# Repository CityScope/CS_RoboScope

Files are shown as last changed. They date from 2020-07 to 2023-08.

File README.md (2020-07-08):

# RoboScope

RoboScop project is an motorize platform and three-dimensional interactive simulation platform for the understanding of urban environments. The platform is made of an array of 3D Pixels that can be configured in varying heights and color to represent different urban conditions. In addition, each pixel

## Circuits

Circuits designs in Eagle

## Code

Source code to run the each one of the different project components, server, client, control and interface.

## Docs

Folder includes designs files, drawings, technical data-sheets, and assembly instructions.

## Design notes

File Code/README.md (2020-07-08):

# Source

Source code for each one of the following components:

- Interface App

  Interface Apps are the applications that act as an interpreter between the physical table and the digital platform. The applications have two versions: a standalone WebApp and a local application in Processing or openFrameworks.

- Hardware

  Code that runs on the physical hardware such as motor control modules, server can bus module, and test code to test hardware.

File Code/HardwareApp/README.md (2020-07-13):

# Hardware Apps

Arduino

## Translator App

Application that manages and translates grid information to the motor modules.

## Module App

Client application for each board.

## Libraries

List of Arduino libraries

- SX1509
- NeoPixel
- CAN Bus FD FlexCAN

## Test Code

- CanBus

- EnableMotor

- NeoPixel

- MotorTest

- InteractionTest

### CAN Bus Protocol

- 11-bit Motor id identifier
- CAN Bus Message - 4 byte Protocol
  - 2 byte RGBW Color
  - 1 byte Motor position
  - 1 byte interaction

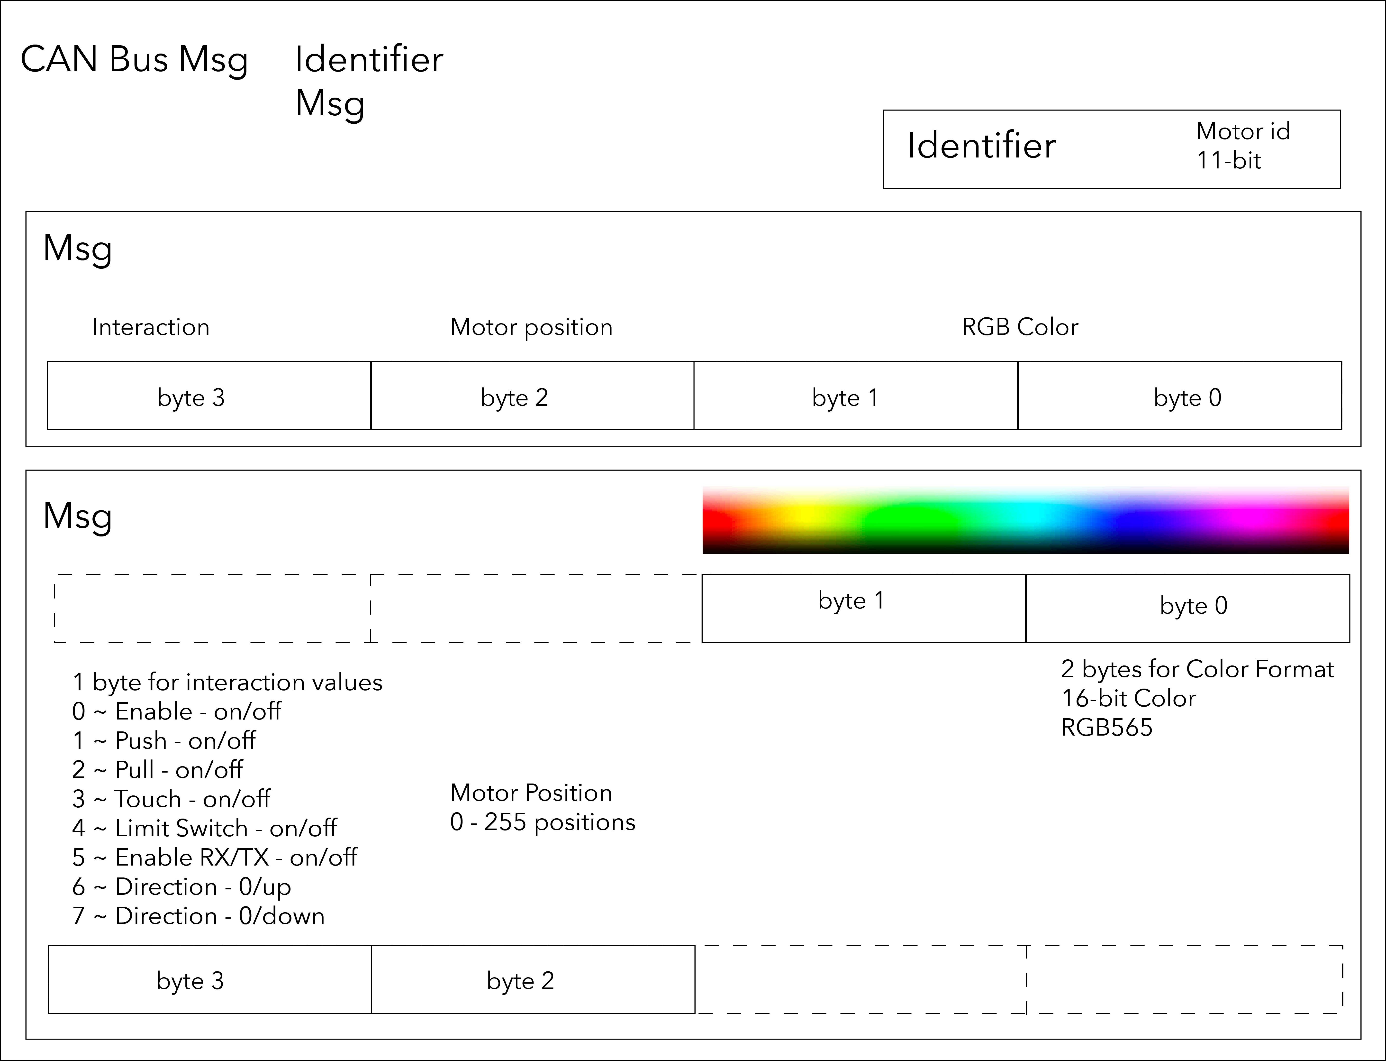
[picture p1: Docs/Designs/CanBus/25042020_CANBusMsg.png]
CAN Bus Block


Server will

  - Board id
    - [id] -> uint32_t
    - ````4 bytes -> [0-4294967295] or [0x00000000-0xFFFFFFFF]````
  - Message
    - buf[8] -> uint8_t array length 8
    - ````1 byte -> [0-255] or [0x00-0xFF]````
      - [0] - Motor id [0, 255]
          - Local id depending on the number of motors on the board
      - [1] - Motor dir - up/down
      - [2] - Motor step  - number of steps
      - [3] - Motor time activation
      - [4] - Motor enable/sleep/activation
      - [5] - Motor limit switches and push and pull
          - ```[0000LHDU]```
          - Limit switch up   (U)    ```[0000000U]```
          - Limit switch down (D)    ```[000000D0]```
          - Push Interaction (Push)  ```[00000H00]```
          - Pull Interaction (Pull)  ```[0000L000]```
      - [6] - Motor sensor 0
      - [7] - Motor sensor 1

### Library:

  - CAN Bus FD and CAN Bus 2.0 for  Teensy 4.0
    https://github.com/tonton81/FlexCAN_T4

  - Data Structure:
    CAN Bus 2.0
    https://github.com/collin80/FlexCAN_Library

  - CAN Bus FD - MCP2562FD
    https://www.microchip.com/wwwproducts/en/MCP2562FD

### Refereces:

  https://github.com/skpang/Teensy40_triple_CAN_demo/blob/master/Teensy40_triple_CAN_demo.ino

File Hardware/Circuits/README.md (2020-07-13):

#  PCB design

## Motors driver

- Teensy 4.0
  - https://www.pjrc.com/store/teensy40.html
- 8 Stepper Motor Drivers
  - DRV8880
  - https://www.pololu.com/product/2971
- Two voltage inputs
  - 12V Input
  - 5V Input, Voltaje protection
- CAN Bus FD  JST Input/Output
  - https://www.digikey.com/short/zb3m2n
- CAN Bus 2.0 JST Input/Output
  - https://www.digikey.com/short/zb3mwz
- SX1509 Multiplexer
  - https://www.sparkfun.com/products/13601
- On/Off Switch

## Interface

- 8x Push Buttons
- 8x 6 Pin JST 1mm
- 3x SX1509 Multiplexer
- Dip Switches

## LED Box

- 4 RGBW LEDs, SK6812
- 2 Push buttons
- JST 1mm

## Translator

- JST 6 pin limit output 1mm
- 4 Key buttons
- CAN Bus 2.0 JST Input/Output
  - https://www.digikey.com/short/zb3mwz
- SX1509 Multiplexer
  - https://www.sparkfun.com/products/13601

## Stepper Counter

- Switch
- JST 1mm
-

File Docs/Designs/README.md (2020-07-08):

# Design files

Core

Fusion 360

## v.02

### Base

- Adjust spacing of the holes of the base
- Adjust the base for each motor, opening for each motor, cable pass for each motors

## Aesthetics

- Box design

### Interface Box

- Redesign the box

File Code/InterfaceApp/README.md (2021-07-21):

## CS CityScope JS

Application in js that allows users to examine different urban-design alternatives and observe their impact through different KPIs and matrices.

### Instructions

##### Running CityScope JS
To run the web application, you can go to the [CityScope JS](https://cityscope.media.mit.edu/CS_cityscopeJS/) website or download/clone the repo here and run the app locally.

To run the app locally, run `npm install` inside the folder to install all the packages and then run `npm start`. For more documentation, go to [CityScope ](https://cityscope.media.mit.edu) website.

##### Roboscope path

`http://localhost:3000/cityscope=roboscope`

##### Setting Up Table Controller
1. Download/clone repo and `cd` into DigitalControls in Terminal
2. Install packages
    1. python-socketio version 4.5.1
    2. flask-socketio 4.3.0
      `pip install python-socketio==4.5.1`
      `pip install flask-socketio==4.3.0`
    2. eventlet version 0.25.2
    3. Flask
3. Connect Teensy table server
4. In `grid_handling.py` change `com_port` to port connected to table server
5. Run `python3 websocketServer.py`

## Virtual Serial Port

Create a virtual port to test communication between the WebSocket and the serial port.

### Mac

`pip3 install PyVirtualSerialPorts`

## Create a Virtual Port

`python3 -m virtualserialports 1`

`ls /dev/cu.*`

## Blocks App

Application in Processing that simulates the physical table

## MovingLegosServer App

Application in openFrameworks that simulates the physical table

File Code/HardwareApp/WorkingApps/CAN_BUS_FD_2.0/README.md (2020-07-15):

## A working implementation of the CAN Bus Protocol 

This implementation of the CAN bus protocol has two parts: server and client. Each utilizes a Message class that was created with the data protocol designed for the Roboscope table. 

### Message Class

The message class provides a seamless way to customize and format CAN bus messages before they are sent to the client or to the server. The following outlines the functions of the class and their uses:
 
- `CANMotorMessage(panel_id, msg_size = 8)`: initializes a CAN bus message with a give panel (node) ID, the msg_size determines whether to send a CAN_FD msg or CAN 2.0 msg
- `addMessage(des, color[], steps, interaction)`: adds 4 bytes of data (color, motor steps, and interaction byte) to its appropriate spot in the message buffer array as determined by the specific motor ID the data is referring to
- `getCANmessage()`: returns a CAN bus message that can then be written to a client

### CANFD_Server

The server writes CAN bus message to the client. The current program sets up CAN bus FD and 2.0, initializes input (button) and output (LED) features, and sends a hardcoded CAN bus message to the client on a button press. 

### CANFD_Client

The client reads CAN bus message from the server. The current program sets up CAN bus FD and 2.0, initializes input (button) and output (LED) features, and prints out all CAN bus messages when received from the server

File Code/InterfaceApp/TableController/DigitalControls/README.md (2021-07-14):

# Web Socket Server

This server is the layer of communication between the Interface App and the physical Roboscope table. The server uses web sockets to send and receive data to and from the Interface App and uses serial communication with the Translator Teensy. Current functionality allows grid updates from the JS Interface while 'brushing' edit events occur to be sent to Translator and continuous reading of data from Translator.

## websocketServer.py

This main server file sets up communication with and runs the sockets that connect to the Interface App. For more information about sockets and socket.io, check out the documentation for the [python-socketio library](https://python-socketio.readthedocs.io/en/latest/)

## grid_handling.py

This file is for all computation and data processing methods needed to be able to send the proper data to either the InterfaceApp or the physical table.

## Install & run

-   run `$ npm install`

-   pyhon 3.3, install Flask, socketio

    `$ pip install flask`

    `$ pip install socketio, python-socketio`

    `$ pip install eventlet, npm, colour, gevent`

-   Run the server with `python websocketServer.py`

Connect to roboscope:

http://localhost:3000/cityscope=roboscope

### Troubleshooting

- Kill Process:

Find the process using port 8080:

`sudo lsof -i:8080`

Kill the process on that port:

`kill $PID`

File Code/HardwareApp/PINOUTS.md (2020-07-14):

# PINOUTS

The pinouts for all the hardware components to be used in code.

## Wiring guide for connecting the motors to the motor control Board

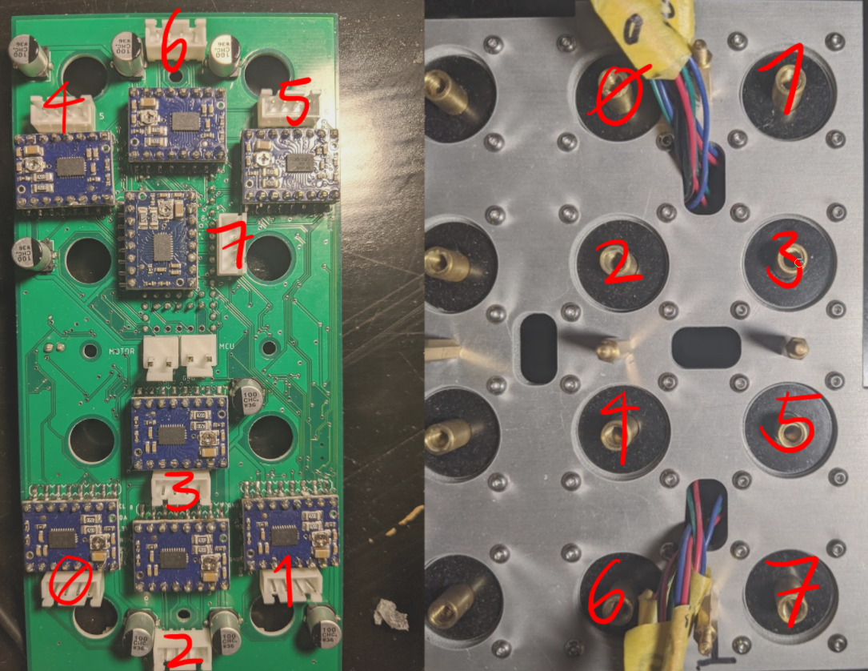
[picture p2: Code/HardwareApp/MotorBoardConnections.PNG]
Motor Wiring Guide


## Pinouts per pixel

| | **Pixel** |  0 |  1 |  2 |  3 |  4 |  5 |  6 |  7 |
|:---:|:---:|:--:|:--:|:--:|:--:|:--:|:--:|:--:|:--:|
| **Pin** | | | | | | | | | |
| Motor Direction | |  6 |  8 | 10 | 15 | 17 | 21 | 23 | 25 |
| Motor Step | |  5 |  7 |  9 | 14 | 16 | 20 | 22 | 24 |
| SX1509 Limit Switch | | 15 | 14 | 13 | 12 | 11 | 10 |  9 |  8 |
| SX1509 Interaction Switch | |  7 |  6 |  5 |  4 |  3 |  2 |  1 |  0 |

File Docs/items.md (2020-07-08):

## List

8/18

Final list of items to buy:
https://docs.google.com/spreadsheets/d/1OweoeCU06feMGqQnCsFGZUhG3TEGoh_JW88oVjHfxHk/edit#gid=0

### Base

- design files of the base
- matrix design files
- Rubber Bushings for base
- screws for motors
- acrylic for top
- aluminum plate for the matrix
- aluminum plate for bottom plate (electronics)
- 3d model of the spacer

Instead of matrix grid approach for the base, Kent suggest we should do horizontal or vertical modules, for easier remove, adjust and plug-play approach.

### Rods/Box

- switches
  - https://www.mouser.com/ProductDetail/653-D2F-01L2-T
- LEDs RGBW
  - NeoPixel:
    https://www.adafruit.com/product/2758
- qwiic cables JST-4 Cable
- 3d Model of the Box
- sensor to detect touch
- Pull/Push interaction

## Energy

Teensy module
  - 4 Amps

## Controls

 - Voltage Control:
   - Arduino ->
   - LEDs
   - Motor
   - Sensors

 - Motor control https://www.sparkfun.com/products/12779
    - STEP    -> GPIO Arduino
    - DIR    -> GPIO Arduino
    - ENABLE -> GPIO Arduino
    - MS1 -> switch GND or 5V
    - MS2 -> switch GND or 5V
    - Voltage IN  -> Power supply range from 6V to 30V.
    - Voltage OUT -> regulated 5V

- Motor Driver:
    - STSPIN220 Low-Voltage Stepper Motor Driver Carrier,  1/256 step https://www.pololu.com/product/2876
    - DRV8834 - 1/32 step https://www.pololu.com/product/2134/specs

 - CAN Bus Protocol (5V, GND)
    - MCP2515  with TJA1050
        - https://harrisonsand.com/static/CAN_module.pdf
    - SCK, MOSI, MISO
    - D13 -> SCK - SCK
    - D12 -> SO  - MISO
    - D11 -> SI  - MOSI
    - D10 -> CS  - ANY
 - swiic cable model
 - voltage input 5V
 - Teensy 3.2 -> CAN BUS, I2C
 - LED for power status
 - switch to turn on/off the motor
 - enumerate each motor and sensor output
      -
 - SAMD21  + 48mhrz
    - https://www.sparkfun.com/products/13664
    - https://www.avdweb.nl/arduino/samd21/samd21-programmer
 - DIP Switch for changing the ID of the motor
    - DIP 10 positions -> 2^9
      https://www.sparkfun.com/products/8034
    - Multiplexer   16 channels
      https://www.sparkfun.com/products/9056
  - CAN Bus Output
  - Switch's Control
      - SparkFun 16 Output I/O Expander Breakout
      - https://www.sparkfun.com/products/13601

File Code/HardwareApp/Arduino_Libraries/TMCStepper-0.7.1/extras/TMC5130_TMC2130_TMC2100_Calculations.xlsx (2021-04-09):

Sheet: Velocity Calculation
This spreadsheet allows the calculation of target velocity and acceleration values for the internal ramp generator of the TMC5130
Usage: | 1. First enter the highlighted values in Parameters and settings
 | 2. Now you can use one of the calculations (1. - 4.) by entering the known parameters (green)
Parameters and settings
 | 150 | RPM | Desired Velocity | t | = | 2^24/fCLK | = | 1.048576 | [sec]
 | 16 | µS/FS | µStepresolution (256) | VMAX | = | 0 … 2^23-512 |  | [µS/t]
 | 1.8 | ° | Fullstep angel | fCLK | = | 16000000 |  | Hz
 | 200 | FS/360° | Fullsteps per revolution
 | 3200 | µS/360° | µSteps per revolution
 | 1 | :1 | gear ratio
1. VMAX to real world units
 | 8388.608 | VMAX | [µS/t] | <--Entry desired VMAX setting here!
 | 2.50 | RPS | motor shaft
 | 900.00 | deg/sec | motor shaft
 | 900.00 | deg/sec | gear box out
 | 8000.00 | Hz | [µSteps/s]
 | 2.50 | RPS | gear box out
2. real world units to VMAX
 | 2.50 | RPS | motor shaft | <--Entry desired rotations per second here!
 | 900.00 | deg/sec | motor shaft
 | 8388.608 | VMAX | [µS/t]
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

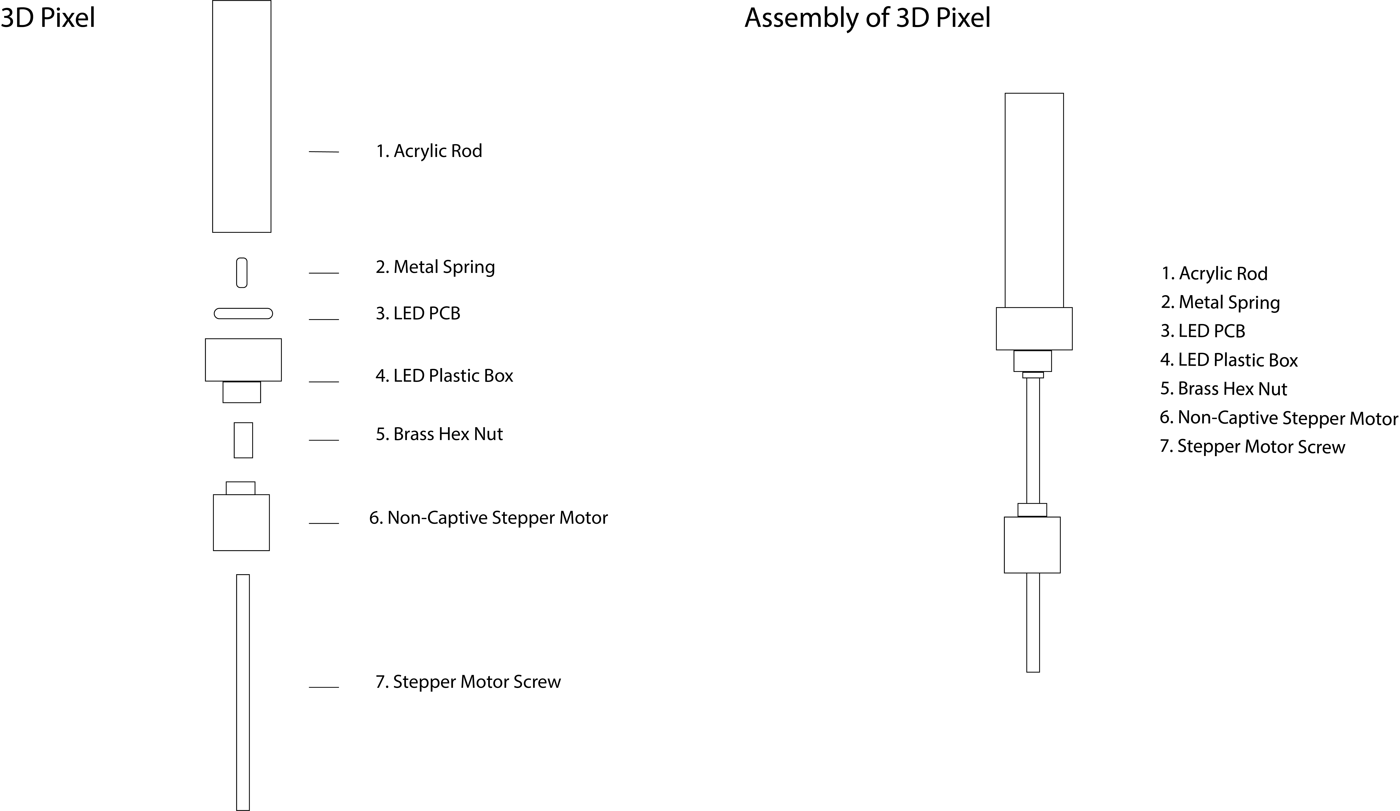
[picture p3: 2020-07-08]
Docs/Designs/Grids/25042020_UrbanPixelDesign.png

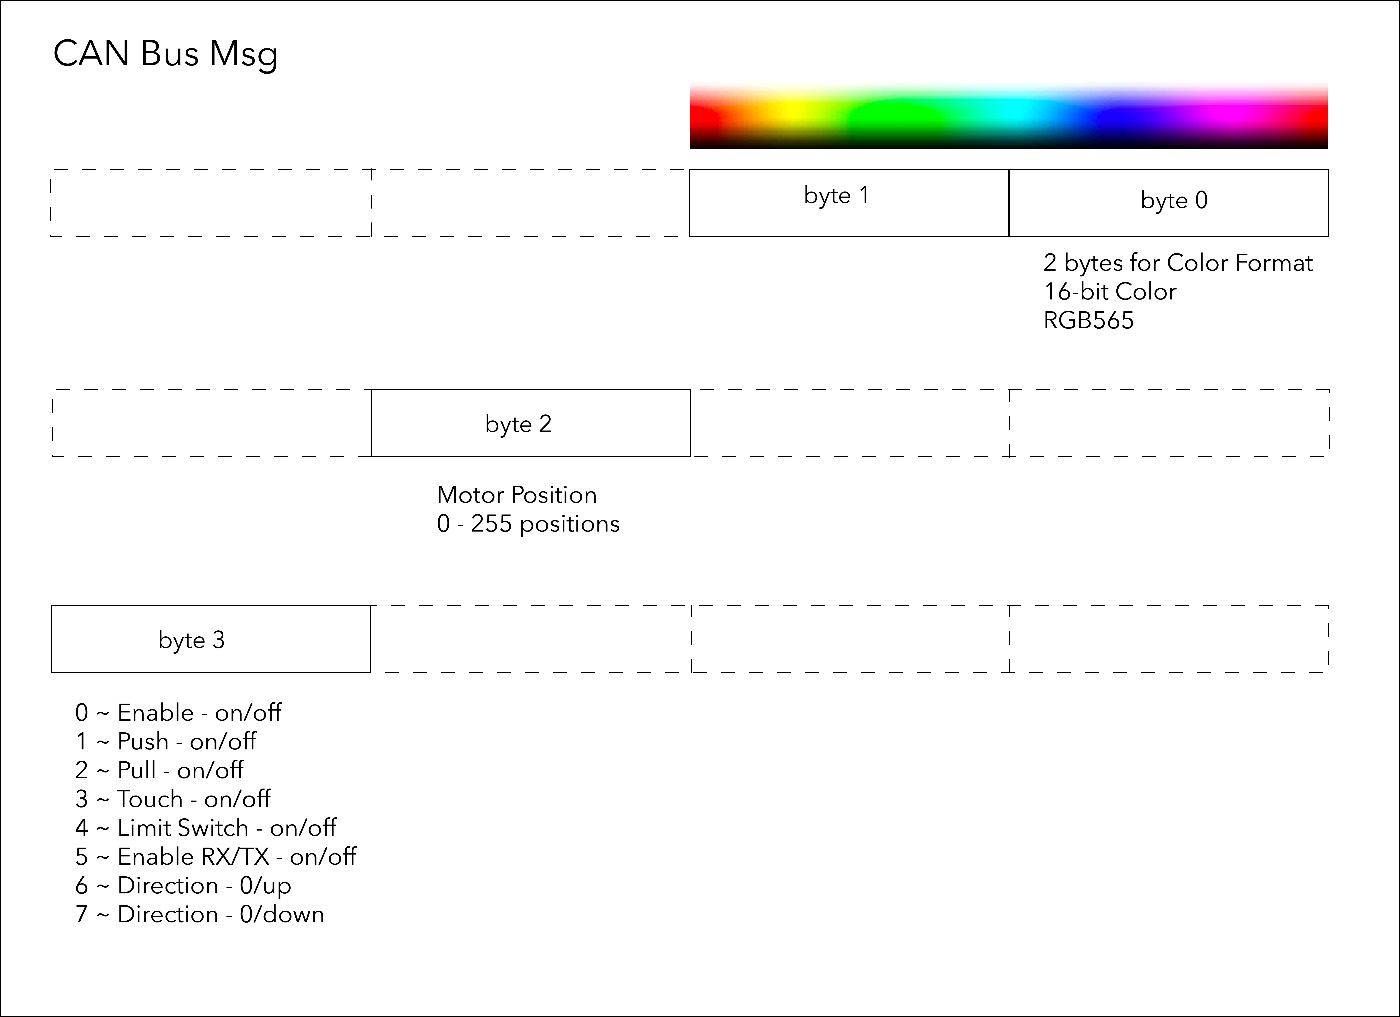
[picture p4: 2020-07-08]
Docs/Designs/CanBus/25042020_CANBusData.png

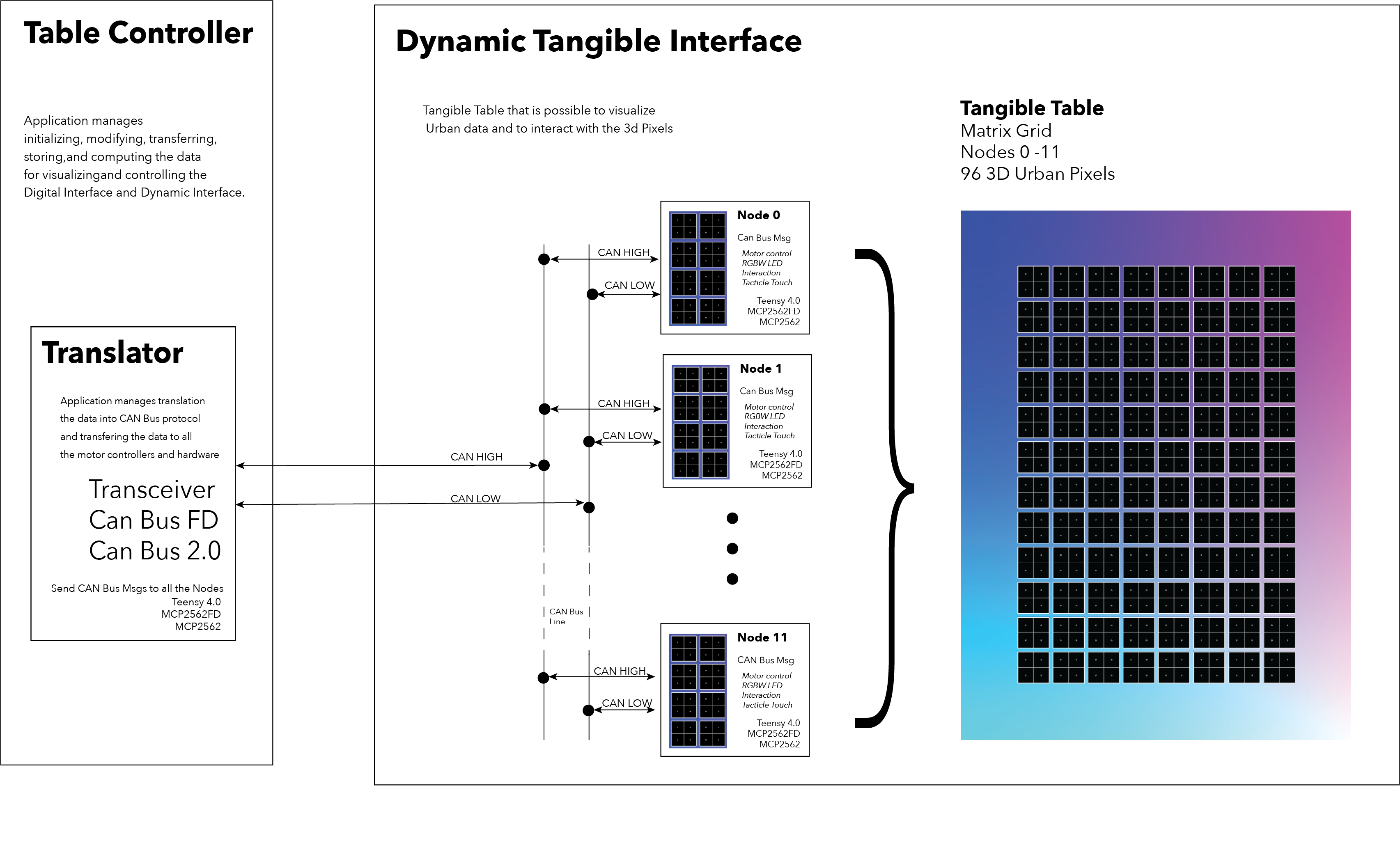
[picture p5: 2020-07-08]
Docs/Designs/communitcation.png

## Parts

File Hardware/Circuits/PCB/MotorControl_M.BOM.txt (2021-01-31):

Partlist exported from /Users/thomas/Documents/RoboScope/CS_RoboScope/Hardware/Circuits/PCB/MotorControl_M.sch at 1/24/21 11:08 PM

Qty Value                           Device                          Package                         Parts                                                                          Description                                                                                                     AVAILABILITY DESCRIPTION                          MF        MP           MPN OC_FARNELL OC_NEWARK PACKAGE        POPULARITY PRICE PROD_ID    PURCHASE-URL                                                  SF_ID     VALUE 
2                                   CONN_02                         1X02                            J2, J3                                                                         Multi connection point. Often used as Generic Header-pin footprint for 0.1 inch spaced/style header connections                                                                                                                                                                                                                            
4                                   CONN_02-JST-2MM-SMT             JST-2-SMD                       CAN_INPUT, CAN_INPUT1, CAN_INPUT4, CAN_INPUT5                                  Multi connection point. Often used as Generic Header-pin footprint for 0.1 inch spaced/style header connections                                                                                                                                   CONN-11443                                                                               
2                                   CONN_06SMD-1MM                  1X06-1MM                        J1, J4                                                                         Multi connection point. Often used as Generic Header-pin footprint for 0.1 inch spaced/style header connections                                                                                                                                   CONN-08249                                                               GPS-00579       
2   0.1uF                           0.1UF-0603-25V-(+80/-20%)       0603                            C8, C11                                                                        0.1µF ceramic capacitors                                                                                                                                                                                                                          CAP-00810                                                                          0.1uF 
3   0.1uF                           0.1UF-25V(+80/-20%)(0603)       0603-CAP                        C2, C3, C9                                                                     CAP-00810                                                                                                                                                                                                                                         CAP-00810                                                                          0.1uF 
5   0.1uf                           0.1UF-25V(+80/-20%)(0603)       0603-CAP                        C4, C5, C6, C7, C10                                                            CAP-00810                                                                                                                                                                                                                                         CAP-00810                                                                          0.1uF 
1   0.3                             0.3OHM-0805-1/8W-1%             0805                            R1                                                                             0.3Ω resistor                                                                                                                                                                                                                                     RES-11622                                                                          0.3   
1   100                             10KOHM-0603-1/10W-1%            0603                            R12                                                                            10kΩ resistor                                                                                                                                                                                                                                     RES-00824                                                                          10k   
8   100uF                           100UF-POLAR-25V-20%(ELEC)       PANASONIC_D                     MC1, MC2, MC3, MC4, MC5, MC6, MC7, MC8                                         100µF polarized capacitors                                                                                                                                                                                                                        CAP-12547                                                                          100uF 
1   10K                             0.3OHM-0805-1/8W-1%             0805                            R20                                                                            0.3Ω resistor                                                                                                                                                                                                                                     RES-11622                                                                          0.3   
1   10K                             10KOHM-0603-1/10W-1%            0603                            R13                                                                            10kΩ resistor                                                                                                                                                                                                                                     RES-00824                                                                          10k   
6   10K                             10KOHM-1/10W-1%(0603)0603       0603-RES                        R2, R3, R5, R6, R9, R11                                                        RES-00824                                                                                                                                                                                                                                         RES-00824                                                                          10K   
2   10k                             10KOHM-0603-1/10W-1%            0603                            R14, R15                                                                       10kΩ resistor                                                                                                                                                                                                                                     RES-00824                                                                          10k   
1   120                             10KOHM-1/10W-1%(0603)0603       0603-RES                        R8                                                                             RES-00824                                                                                                                                                                                                                                         RES-00824                                                                          10K   
1   120Ohms                         10KOHM-1/10W-1%(0603)0603       0603-RES                        R4                                                                             RES-00824                                                                                                                                                                                                                                         RES-00824                                                                          10K   
8   1X04_STRAIGHT                   1X4-CLEANBIG                    1X04-CLEANBIG                   CM_01, CM_02, CM_03, CM_04, CM_05, CM_06, CM_07, CM_08                         4-pin connector                                                                                                                                                                                                                                                                                                                            
1   47uf/10V                        0.1UF-25V(+80/-20%)(0603)       0603-CAP                        C1                                                                             CAP-00810                                                                                                                                                                                                                                         CAP-00810                                                                          0.1uF 
1   500                             10KOHM-1/10W-1%(0603)0603       0603-RES                        R10                                                                            RES-00824                                                                                                                                                                                                                                         RES-00824                                                                          10K   
1   74AHC1G125FDBV                  74AHC1G125FDBV                  SOT23-5                         IC1                                                                            Single Bus Buffer Gate with 3-State Output                                                                                                                                                                                       0                                                                                                         
2   74HC4051BQ                      74HC4051BQ                      DHVQFN-16-2.5X3.5MM             U3, U4                                                                         NXP 74HC4051 8-Channel Analog Multiplexer/Demultiplexer                                                                                                                                                                                           IC-13334                                                                                 
2   B2P-VH                          B2P-VH                          B2P-VH                          POWER_M, POWER_MCU                                                             JST VH Series header 3.96mm pitch disconnectable crimp style connectors, vertical (side entry type), 2 pins                                                                                                                                                                                                                                
8   DRV8880                         DRV8880                         DRV8880                         MOTOR_01, MOTOR_02, MOTOR_03, MOTOR_04, MOTOR_05, MOTOR_06, MOTOR_07, MOTOR_08                                                                                                                                                                                                                                                                                                                                            
2   JUMPER-SMT_2_NC_TRACE_NO-SILK   JUMPER-SMT_2_NC_TRACE_NO-SILK   SMT-JUMPER_2_NC_TRACE_NO-SILK   JP5, JP6                                                                       Normally closed trace jumper                                                                                                                                                                                                                                                                                                               
1   LEDFAB1206                      LEDFAB1206                      LED1206FAB                      STATUS_LED                                                                     LED                                                                                                                                                                                                                                                                                                                                        
1   M-2X10-87759                    M-2X10-87759                    87759-20                        P1                                                                             MALE HEADER                                                                                                                                                                                                                                                                                                                                
2   MCP2562-E/SN                    MCP2562-E/SN                    SOIC127P600X175-8N              MCP2562FD, MCP2562_2.0                                                         MCP2562 Series 5 V Surface Mount High-Speed CAN Transceiver - SOIC-8 Check prices                               Good          1/1 Transceiver Half CANbus 8-SOIC  Microchip MCP2562-E/SN                          SO-8 Microchip            None             https://pricing.snapeda.com/search/part/MCP2562-E/SN/?ref=eda                 
1   MIC2005                         MIC2005                         SOT23-6                         U1                                                                                                                                                                                                                                                                                                                                                                                                                        
1   MOSFET_SLIDER                   MOSFET_SLIDER                   MOSFET_SLIDER                   U$1                                                                                                                                                                                                                                                                                                                                                                                                                       
2   PESD1CAN                        PESD1CAN                        SOT23                           PES_D3, PES_D5                                                                 CAN bus ESD protection diode                                                                                                                                                                                                     0                                                                                                         
1   S2A                             S2A                             DO214AA                         D1                                                                             S2A - S2M General Purpose Rectifiers                                                                                                                              Fairchild              S2A 1467485    58K2391                                                                                                                            
1   SX1509                          SX1509                          QFN-28                          SX1509                                                                         Semtech SX1509                                                                                                                                                                                                                                    IC-11311                                                                           SX1509
1   TEENSY_4.0_WITH_SMD_HEADER_PINS TEENSY_4.0_WITH_SMD_HEADER_PINS TEENSY_4.0_WITH_SMD_HEADER_PINS U$3                                                                            Footprint for Teensy 3.1 or 3.2 board using all pin connections on the outer perimeter

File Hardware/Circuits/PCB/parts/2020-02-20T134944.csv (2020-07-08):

Index | Quantity | Part Number | Manufacturer Part Number | Description | Customer Reference | Available | Backorder | Unit Price | Extended Price USD
1 | 15 | SMBJ24ALFCT-ND | SMBJ24A | TVS DIODE 24V 38.9V DO214AA |  | 15 | 0 | 0.28900 | 4.34
2 | 15 | SMBJ15ALFCT-ND | SMBJ15A | TVS DIODE 15V 24.4V DO214AA |  | 15 | 0 | 0.27700 | 4.16
3 | 25 | 455-1183-ND | VHR-2N | CONN HOUSING VH 2POS 3.96MM WHT |  | 25 | 0 | 0.07120 | 1.78
4 | 25 | 1727-1306-1-ND | PESD1CAN-UX | TVS DIODE 24V 50V SC70-3 |  | 25 | 0 | 0.26360 | 6.59
5 | 15 | 401-2013-1-ND | AYZ0202AGRLC | SWITCH SLIDE DPDT 100MA 12V | HTTPS://WWW.DIGIKEY.COM/PRODUCT-DETAIL/EN/C-K/AY | 15 | 0 | 1.17000 | 17.55
6 | 15 | CT21910MST-ND | 219-10MST | SWITCH SLIDE DIP SPST 100MA 20V |  | 15 | 0 | 1.02100 | 15.32
7 | 25 | S5676-ND | NPTC062KFMS-RC | CONN HDR 12POS 0.1 TIN SMD |  | 25 | 0 | 1.22800 | 30.70
8 | 100 | 455-1319-1-ND | SVH-41T-P1.1 | CONN SOCKET 16-20AWG CRIMP TIN |  | 100 | 0 | 0.06100 | 6.10
9 | 200 | 399-1099-1-ND | C0603C104M4RACTU | CAP CER 0.1UF 16V X7R 0603 | CM C1 C9 C11 C12 | 200 | 0 | 0.01400 | 2.80
10 | 300 | RNCP0603FTD10K0CT-ND | RNCP0603FTD10K0 | RES 10K OHM 1% 1/8W 0603 |  | 300 | 0 | 0.02300 | 6.90
11 | 100 | RNCP0603FTD499RCT-ND | RNCP0603FTD499R | RES 499 OHM 1% 1/8W 0603 |  | 100 | 0 | 0.02300 | 2.30
12 | 120 | PCE3750CT-ND | EEE-HC1C101XP | CAP ALUM 100UF 20% 16V SMD |  | 120 | 0 | 0.12000 | 14.40
13 | 25 | S9001-ND | SPC02SYAN | CONN JUMPER SHORTING GOLD FLASH |  | 25 | 0 | 0.03800 | 0.95
14 | 20 | SAM8985-ND | TSM-105-01-T-DV | CONN HEADER SMD 10POS 2.54MM |  | 20 | 0 | 0.57300 | 11.46
15 | 15 | CKN12222-1-ND | PTS526 SMG15 SMTR2 LFS | TACT 5.2 X 5.2, 1.5 MM H, 160GF, |  | 15 | 0 | 0.08200 | 1.23
16 | 2 | 1568-DEV-15583-ND | DEV-15583 | TEENSY 4.0 |  | 2 | 0 | 22.50000 | 45.00
17 | 20 | 754-1439-1-ND | APT3216QBC/D | LED BLUE CLEAR CHIP SMD |  | 20 | 0 | 0.30200 | 6.04
18 | 180 | 455-1792-1-ND | BM06B-SRSS-TB(LF)(SN) | CONN HEADER SMD 6POS 1MM |  | 180 | 0 | 0.57970 | 104.35
19 | 30 | S2212EC-06-ND | PREC006DFAN-RC | CONN HEADER VERT 12POS 2.54MM |  | 30 | 0 | 0.20600 | 6.18
20 | 15 | S6105-ND | PPTC052LFBN-RC | CONN HDR 10POS 0.1 TIN PCB |  | 15 | 0 | 0.51400 | 7.71
21 | 15 | MCP2562FD-E/SN-ND | MCP2562FD-E/SN | IC TRANSCEIVER 1/1 8SOIC |  | 15 | 0 | 0.96000 | 14.40
22 | 15 | MCP2562-E/SN-ND | MCP2562-E/SN | IC TRANSCEIVER HALF 1/1 8SOIC |  | 15 | 0 | 0.90000 | 13.50
23 | 15 | LTC4359CMS8#PBF-ND | LTC4359CMS8#PBF | IC OR CTRLR N+1 8MSOP |  | 15 | 0 | 4.34000 | 65.10
24 | 15 | BSC028N06NSATMA1CT-ND | BSC028N06NSATMA1 | MOSFET N-CH 60V 23A TDSON-8 |  | 15 | 0 | 1.63600 | 24.54
25 | 15 | 160-1737-1-ND | LTW-150TK | LED WHITE CHIP SMD |  | 15 | 0 | 0.40400 | 6.06
26 | 30 | RMCF0603FT120RCT-ND | RMCF0603FT120R | RES 120 OHM 1% 1/10W 0603 |  | 30 | 0 | 0.01400 | 0.42
27 | 20 | 311-1.0KGRCT-ND | RC0603JR-071KL | RES SMD 1K OHM 5% 1/10W 0603 |  | 20 | 0 | 0.01700 | 0.34
28 | 20 | 445-174769-1-ND | C1608X7S1C155K080AC | CAP CER 1.5UF 16V X7S 0603 |  | 20 | 0 | 0.13600 | 2.72
29 | 50 | 455-1749-1-ND | S2B-PH-SM4-TB(LF)(SN) | CONN HEADER SMD R/A 2POS 2MM | J9 | 50 | 0 | 0.46500 | 23.25
30 | 100 | P16854CT-ND | EVP-ASAC1A | SWITCH TACTILE SPST-NO 0.05A 12V |  | 100 | 0 | 0.38100 | 38.10
31 | 100 | EG1866-ND | TL1105DF250Q | SWITCH TACTILE SPST-NO 0.05A 12V |  | 100 | 0 | 0.12600 | 12.60
32 | 15 | CKN12245-1-ND | JS207011SCQNR | SWITCH SLIDE DP3T 300MA 6V |  | 15 | 0 | 0.93100 | 13.97
33 | 15 | SMAT70A-FDICT-ND | SMAT70A-13-F | TVS DIODE 70V 100V SMA |  | 15 | 0 | 0.46700 | 7.01
34 | 15 | DDZ9699DICT-ND | DDZ9699-7 | DIODE ZENER 12V 500MW SOD123 |  | 15 | 0 | 0.22400 | 3.36
35 | 100 | 455-1127-1-ND | SPH-002T-P0.5S | CONN SOCKET 24-30AWG CRIMP TIN |  | 100 | 0 | 0.02700 | 2.70
36 | 50 | 455-1165-ND | PHR-2 | CONN HOUSING PH 2POS 2MM WHITE |  | 50 | 0 | 0.05000 | 2.50
37 | 120 | 455-2249-ND | B4B-XH-A(LF)(SN) | CONN HEADER VERT 4POS 2.5MM |  | 120 | 0 | 0.11500 | 13.80
38 | 2 | Z6363CT-ND | EE-SX1320 | SENSOR OPT SLOT PHOTOTRANS MODUL |  | 2 | 0 | 1.18000 | 2.36
39 | 2 | 1855-1009-ND | GP1S094HCZ0F | SENSOR OPT SLOT PHOTOTRAN PCB MT |  | 2 | 0 | 0.60000 | 1.20
40 | 2 | 846-1021-ND | RPI-441C1E | SENSOR OPT SLOT TRANSISTOR MODUL |  | 2 | 0 | 1.09000 | 2.18
41 | 16 | 455-3007-ND | A06SR06SR30K305A | JUMPER 06SR-3S - 06SR-3S 12" |  | 16 | 0 | 1.54300 | 24.69
42 | 25 | MCP2562FD-H/SN-ND | MCP2562FD-H/SN | IC TRANSCEIVER 1/1 8SOIC |  | 25 | 0 | 0.87000 | 21.75

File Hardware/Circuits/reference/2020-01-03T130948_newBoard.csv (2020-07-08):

Index | Quantity | Part Number | Manufacturer Part Number | Description | Customer Reference | Available | Backorder | Unit Price | Extended Price USD
1 | 4 | 1727-7258-1-ND | BUK768R3-60E,118 | MOSFET N-CH 60V 75A D2PAK |  | 4 | 0 | 1.14000 | 4.56
2 | 5 | SMBJ24ALFCT-ND | SMBJ24A | TVS DIODE 24V 38.9V DO214AA |  | 5 | 0 | 0.39000 | 1.95
3 | 5 | SMBJ15ALFCT-ND | SMBJ15A | TVS DIODE 15V 24.4V DO214AA |  | 5 | 0 | 0.37000 | 1.85
4 | 5 | 296-43067-1-ND | LM74610QDGKRQ1 | IC SMART DIODE CTLR 8VSSOP |  | 5 | 0 | 2.05000 | 10.25
5 | 10 | 455-1183-ND | VHR-2N | CONN HOUSING VH 2POS 3.96MM WHT |  | 10 | 0 | 0.09600 | 0.96
6 | 10 | 455-1133-1-ND | SVH-21T-P1.1 | CONN SOCKET 18-22AWG CRIMP TIN |  | 10 | 0 | 0.10700 | 1.07
7 | 15 | SX1509BIULCT-ND | SX1509BIULTRT | IC GPIO EXPANDER I2C 16CH 28QFN |  | 15 | 0 | 1.85700 | 27.86
8 | 10 | 1727-1306-1-ND | PESD1CAN-UX | TVS DIODE 24V 50V SC70-3 |  | 10 | 0 | 0.29500 | 2.95
9 | 10 | 2183-2971-ND | 2971 | DRV8880 STEPPER MTR DRVR CARRIER |  | 10 | 0 | 6.95000 | 69.50
10 | 10 | 401-2013-1-ND | AYZ0202AGRLC | SWITCH SLIDE DPDT 100MA 12V | HTTPS://WWW.DIGIKEY.COM/PRODUCT-DETAIL/EN/C-K/AY | 10 | 0 | 1.17000 | 11.70
11 | 10 | 296-26344-1-ND | SN65HVD232DR | IC TRANSCEIVER HALF 1/1 8SOIC |  | 10 | 0 | 1.53100 | 15.31
12 | 10 | CT21910MST-ND | 219-10MST | SWITCH SLIDE DIP SPST 100MA 20V |  | 10 | 0 | 1.02100 | 10.21
13 | 10 | S5675-ND | NPTC052KFMS-RC | CONN HDR 10POS 0.1 TIN SMD |  | 10 | 0 | 0.98500 | 9.85
14 | 20 | S5676-ND | NPTC062KFMS-RC | CONN HDR 12POS 0.1 TIN SMD |  | 20 | 0 | 1.22800 | 24.56
15 | 10 | 455-3990-ND | VHR-4M | CONN HOUSING VH 4POS 3.96MM WHT |  | 10 | 0 | 0.14500 | 1.45
16 | 10 | 455-1650-ND | B4PS-VH(LF)(SN) | CONN HEADER R/A 4POS 3.96MM |  | 10 | 0 | 0.28700 | 2.87
17 | 100 | 455-1319-1-ND | SVH-41T-P1.1 | CONN SOCKET 16-20AWG CRIMP TIN |  | 100 | 0 | 0.06100 | 6.10
18 | 10 | SAM1048-06-ND | TSW-106-08-T-D | CONN HEADER VERT 12POS 2.54MM |  | 10 | 0 | 0.58100 | 5.81
19 | 100 | 1276-1183-1-ND | CL10A225KQ8NNNC | CAP CER 2.2UF 6.3V X5R 0603 |  | 100 | 0 | 0.02900 | 2.90
20 | 200 | 399-1099-1-ND | C0603C104M4RACTU | CAP CER 0.1UF 16V X7R 0603 | CM C1 C9 C11 C12 | 200 | 0 | 0.01400 | 2.80
21 | 100 | 1276-1907-1-ND | CL10A475MQ8NNNC | CAP CER 4.7UF 6.3V X5R 0603 |  | 100 | 0 | 0.02100 | 2.10
22 | 200 | RNCP0603FTD10K0CT-ND | RNCP0603FTD10K0 | RES 10K OHM 1% 1/8W 0603 |  | 200 | 0 | 0.02300 | 4.60
23 | 100 | RNCP0603FTD499RCT-ND | RNCP0603FTD499R | RES 499 OHM 1% 1/8W 0603 |  | 100 | 0 | 0.02300 | 2.30
24 | 100 | 541-60.4HCT-ND | CRCW060360R4FKEA | RES SMD 60.4 OHM 1% 1/10W 0603 |  | 100 | 0 | 0.01390 | 1.39
25 | 30 | PCE3750CT-ND | EEE-HC1C101XP | CAP ALUM 100UF 20% 16V SMD |  | 30 | 0 | 0.12000 | 3.60
26 | 25 | S9001-ND | SPC02SYAN | CONN JUMPER SHORTING GOLD FLASH |  | 25 | 0 | 0.03800 | 0.95
27 | 100 | 455-2243-ND | S4B-XH-A(LF)(SN) | CONN HEADER R/A 4POS 2.5MM |  | 100 | 0 | 0.15200 | 15.20
28 | 20 | SAM8985-ND | TSM-105-01-T-DV | CONN HEADER SMD 10POS 2.54MM |  | 20 | 0 | 0.57300 | 11.46
29 | 25 | CKN12222-1-ND | PTS526 SMG15 SMTR2 LFS | TACT 5.2 X 5.2, 1.5 MM H, 160GF, |  | 25 | 0 | 0.07920 | 1.98
30 | 2 | 1568-DEV-15583-ND | DEV-15583 | TEENSY 4.0 |  | 2 | 0 | 22.50000 | 45.00
31 | 10 | 296-29408-1-ND | CD74HC4067M96 | IC MUX/DEMUX 1X16 24SOIC |  | 10 | 0 | 0.59900 | 5.99
32 | 10 | MCP2562FDT-E/SNCT-ND | MCP2562FDT-E/SN | IC TRANSCEIVER 1/1 8SOIC |  | 10 | 0 | 0.96000 | 9.60
33 | 10 | MCP2562-E/SN-ND | MCP2562-E/SN | IC TRANSCEIVER HALF 1/1 8SOIC |  | 10 | 0 | 0.90000 | 9.00
34 | 20 | 754-1439-1-ND | APT3216QBC/D | LED BLUE CLEAR CHIP SMD |  | 20 | 0 | 0.30200 | 6.04
35 | 2 | 1528-1710-ND | 2759 | ADDRESS LED DISC SER RGBW 1=10 |  | 2 | 0 | 5.95000 | 11.90
36 | 30 | 455-1792-1-ND | BM06B-SRSS-TB(LF)(SN) | CONN HEADER SMD 6POS 1MM |  | 30 | 0 | 0.67200 | 20.16
37 | 30 | 455-1806-1-ND | SM06B-SRSS-TB(LF)(SN) | CONN HEADER SMD R/A 6POS 1MM |  | 30 | 0 | 0.78200 | 23.46
38 | 25 | 455-3019-ND | A06SR06SR30K305B | JUMPER 06SR-3S - 06SR-3S 12" |  | 25 | 0 | 1.44800 | 36.20

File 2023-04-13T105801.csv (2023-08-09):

Index | Quantity | Part Number | Manufacturer Part Number | Description | Customer Reference | Available | Backorder | Unit Price | Extended Price USD
1 | 50 | 311-1776-1-ND | CC0603JRX7R7BB104 | CAP CER 0.1UF 16V X7R 0603 |  | 50 | 0 | 0.03100 | 1.55
2 | 50 | 1276-1854-1-ND | CL32A106KAULNNE | CAP CER 10UF 25V X5R 1210 |  | 50 | 0 | 0.12800 | 6.40
3 | 10 | 929984-01-36-ND | 929984-01-36 | CONN RCPT 36POS 0.1 TIN-LEAD PCB | 10 | 10 | 0 | 4.13000 | 41.30
4 | 40 | S5600-ND | NPTC081KFXC-RC | CONN HDR 8POS 0.1 TIN SMD |  | 40 | 0 | 0.86500 | 34.60
5 | 3 | 612-MTMM-140-07-F-D-260-ND | MTMM-140-07-F-D-260 | CONN HDR 2MM PCB VERT |  | 3 | 0 | 11.47000 | 34.41
6 | 4 | 17-2-2314844-0-ND | 2-2314844-0 | CONN RCPT 20 POS 0.079" GOLD SMD |  | 4 | 0 | 1.68000 | 6.72
7 | 4 | 3-1470209-3-ND | 3-1470209-3 | CONN RCPT 20POS 0.079 GOLD PCB |  | 4 | 0 | 0.97000 | 3.88
8 | 6 | SX1509BIULCT-ND | SX1509BIULTRT | IC XPNDR 400KHZ I2C 28QFN |  | 6 | 0 | 3.02000 | 18.12
9 | 20 | A129677CT-ND | CRGCQ0603F120R | CRGCQ 0603 120R 1% |  | 20 | 0 | 0.02700 | 0.54
10 | 30 | A100080CT-ND | 1775469-2 | CONN HEADER SMD R/A 2POS 2MM |  | 30 | 0 | 0.66900 | 20.07
11 | 55 | S310FACT-ND | S310FA | DIODE SCHOTTKY 100V 3A SOD123FA |  | 55 | 0 | 0.45600 | 25.08
12 | 100 | 541-3949-1-ND | CRCW06031K00FKEAC | RES SMD 1K OHM 1% 1/10W 0603 |  | 100 | 0 | 0.01200 | 1.20
13 | 100 | A106047CT-ND | CRG0603F100R | RES SMD 100 OHM 1% 1/10W 0603 |  | 100 | 0 | 0.01100 | 1.10
14 | 100 | 1276-1019-1-ND | CL10B105KO8NNNC | CAP CER 1UF 16V X7R 0603 |  | 100 | 0 | 0.01600 | 1.60
15 | 10 | 576-2587-1-ND | MIC2005-0.8YM6-TR | IC PWR SWITCH P-CHAN 1:1 SOT23-6 |  | 10 | 0 | 1.04000 | 10.40
16 | 40 | EG1866-ND | TL1105DF250Q | SWITCH TACTILE SPST-NO 0.05A 12V |  | 40 | 0 | 0.18200 | 7.28
17 | 40 | P124212CT-ND | EVP-ASKC1A | SWITCH LIGHT TOUCH 3.0N NO SMD |  | 40 | 0 | 0.46920 | 18.77
18 | 5 | 1830-1090-1-ND | IN-S126AT5UW | LED WHITE CLEAR 1206 SMD |  | 5 | 0 | 0.32000 | 1.60
19 | 5 | 732-4989-1-ND | 150120BS75000 | LED BLUE CLEAR 1206 SMD |  | 5 | 0 | 0.20000 | 1.00
20 | 6 | 1727-5163-1-ND | PESD1FLEX,215 | TVS DIODE 24VWM 70VC TO236AB |  | 6 | 0 | 0.31000 | 1.86
21 | 40 | 455-2249-ND | B4B-XH-A(LF)(SN) | CONN HEADER VERT 4POS 2.5MM |  | 40 | 0 | 0.16100 | 6.44
22 | 100 | A106048CT-ND | CRG0603F10K | RES SMD 10K OHM 1% 1/10W 0603 |  | 100 | 0 | 0.01100 | 1.10
23 | 40 | 455-1806-1-ND | SM06B-SRSS-TB(LF)(SN) | CONN HEADER SMD R/A 6POS 1MM | MASTER_V2 | 40 | 0 | 0.57700 | 23.08
24 | 10 | 296-53378-1-ND | DRV5032DUDBZT | MAGNETIC SWITCH UNIPOLAR SOT23-3 |  | 10 | 0 | 0.96700 | 9.67
25 | 6 | 296-8404-1-ND | SN74HCT245PWR | IC TXRX NON-INVERT 5.5V 20TSSOP |  | 6 | 0 | 0.46000 | 2.76
26 | 50 | 10-EEE-FPE101XALCT-ND | EEE-FPE101XAL | CAP ALUM 100UF 20% 25V SMD |  | 50 | 0 | 0.41200 | 20.60
27 | 6 | MCP2562FDT-E/SNCT-ND | MCP2562FDT-E/SN | IC TRANSCEIVER 1/1 8SOIC |  | 6 | 0 | 1.17000 | 7.02
28 | 10 | YC164J-100KCT-ND | YC164-JR-07100KL | RES ARRAY 4 RES 100K OHM 1206 | ARRAY CHIP RESISTOR | 10 | 0 | 0.07500 | 0.75
29 | 5 | CT21910MST-ND | 219-10MST | SWITCH SLIDE DIP SPST 100MA 20V |  | 5 | 0 | 0.95000 | 4.75
30 | 35 | 455-2875-1-ND | BM06B-SRSS-TBT(LF)(SN) | CONN HEADER SMD 6POS 1MM |  | 35 | 0 | 0.71300 | 24.96
31 | 10 | 609-10129383-910002ALFCT-ND | 10129383-910002ALF | CONN HEADER SMD 10POS 2.54MM |  | 10 | 0 | 0.35900 | 3.59

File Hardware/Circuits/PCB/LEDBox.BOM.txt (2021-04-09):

Partlist exported from /Users/thomas/Documents/RoboScope/CS_RoboScope/Hardware/Circuits/PCB/LEDBox.sch at 2/28/21 9:12 PM

Qty Value                                                                Device                                                               Package                            Parts                  Description                                                                                                     AMBIENT_TEMPERATURE_RANGE_HIGH AMBIENT_TEMPERATURE_RANGE_LOW AUTOMOTIVE CENTROID_NOT_SPECIFIED DATASHEET                          DEVICE_CLASS_L1 DEVICE_CLASS_L2  DEVICE_CLASS_L3 DIGIKEY_DESCRIPTION             DIGIKEY_PART_NUMBER FOOTPRINT_PARAMETERS_1                                                                                                                                                                                                                                                                                                                                                                                                                                                                                                                                                                                                                                                                                                                                                                                                                                                                                                                                                                                                                                                                                                                                                                                                                                                                                                                                                                                                                                                                                                                                                                                                                                                                                                                                                                                                                                                                                                                                                                                                                                                                                                                                                                                                                                                                                                                                                                                                                                                                                                                                                                                                                                                    FOOTPRINT_PARAMETERS_2                                                                                                                                                                                                                                                                                                                                                                                                                                                                                                                                                                                                                                                                                                                                                                                                                                                                                                                                                                                                                                                                                                                                                                                                                                                                                                                                                                                                                                                                                                                                                                                                                                                                                                                                                                                                                                                                                                                                                                                                                                                                                                                                                                                                                                                                                                                                                                                                                                                                                                                                                                                                                                                    FOOTPRINT_PARAMETERS_3                                                                                                                                                                                                                                                                                                                                                                                                                                                                                                                                                                                                                                                                                                                                                                                                                                                                                                                                                                                                                                                                                                                                                                                                                                                                                                                                                                                                                                                                                                                                                                                                                                                                                                                                                                                                                                                                                                                                                                                                                                                                                                                                                                                                                                                                                                                                                                                                                                                                                                                                                                                                                                                    FOOTPRINT_VARIANT_NAME_0 FOOTPRINT_VARIANT_NAME_1 FOOTPRINT_VARIANT_NAME_2 FOOTPRINT_VARIANT_NAME_3 HEIGHT LEAD_FREE MAX_JUNCTION_TEMP MAX_SUPPLY_VOLTAGE MF                MFG_PACKAGE_IDENT MFG_PACKAGE_IDENT_COMPONENT_ID MFG_PACKAGE_IDENT_DATE MFG_PACKAGE_IDENT_REV MIN_SUPPLY_VOLTAGE MOUSER_DESCRIPTION                                                                           MOUSER_PART_NUMBER MPN            OPERATING_SUPPLY_CURRENT OUTPUT_CURRENT OUTPUT_VOLTAGE PACKAGE PREFIX PROD_ID    ROHS SENSING_METHOD SF_ID     STANDOFF_HEIGHT TEMPERATURE_RANGE_HIGH TEMPERATURE_RANGE_LOW VERIFICATION_VERSION
1                                                                        CONN_041X04_NO_SILK                                                  1X04_NO_SILK                       J1                     Multi connection point. Often used as Generic Header-pin footprint for 0.1 inch spaced/style header connections                                                                                                                                                                                                                                                                                                                                                                                                                                                                                                                                                                                                                                                                                                                                                                                                                                                                                                                                                                                                                                                                                                                                                                                                                                                                                                                                                                                                                                                                                                                                                                                                                                                                                                                                                                                                                                                                                                                                                                                                                                                                                                                                                                                                                                                                                                                                                                                                                                                                                                                                                                                                                                                                                                                                                                                                                                                                                                                                                                                                                                                                                                                                                                                                                                                                                                                                                                                                                                                                                                                                                                                                                                                                                                                                                                                                                                                                                                                                                                                                                                                                                                                                                                                                                                                                                                                                                                                                                                                                                                                                                                                                                                                                                                                                                                                                                                                                                                                                                                                                                                                                                                                                                                                                                                                                                                                                                                                                                                                                                                                                                                                                                                                                                                                                                                                                                                                                                                                                                                                                                                                                                                                                                                                                                                                                                                                                                                                                                                                                                                                                                                                                                                                                                                                                                                                                                                                                                                                                                                                                                                                                                                                                                                                                                                                                                                                                                                                                                                                                                                                                                                                                                                                                                                                                                                                                                                                                                                                                                                                                                                                                                                                                                                                                                                                                                                                                                                                                                                                                                                                                                                                                                                                                                                                                                                        CONN-09696
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

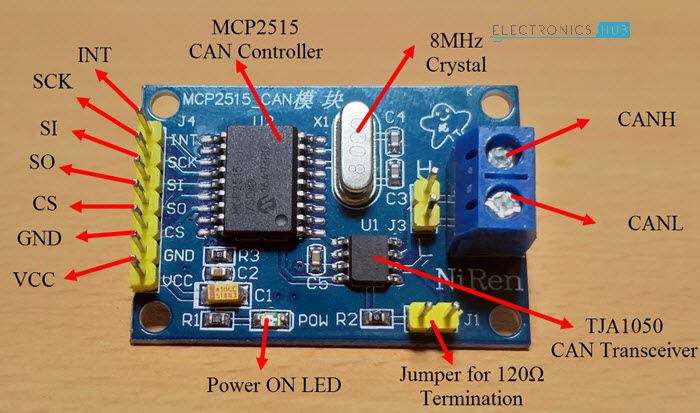
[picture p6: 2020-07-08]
Docs/Designs/CanBus/Arduino-MCP2515-CAN-Bus-Interface-MCP2515-CAN-Module-Components.jpg

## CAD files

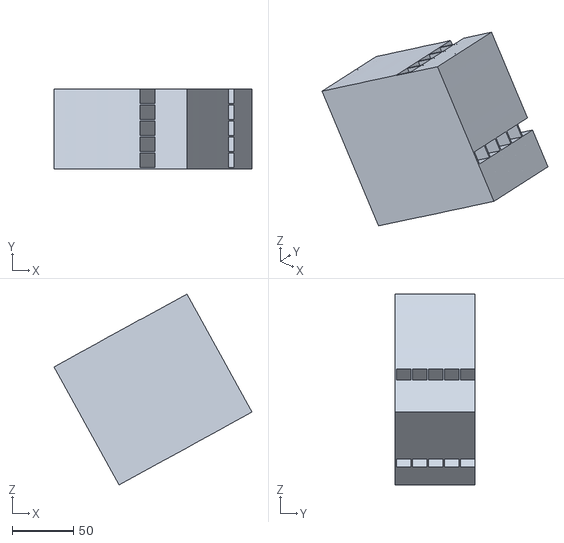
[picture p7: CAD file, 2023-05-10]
Code/InterfaceApp/VolpeExperienceLight/data/A8.obj
161.6 x 65.1 x 155.8

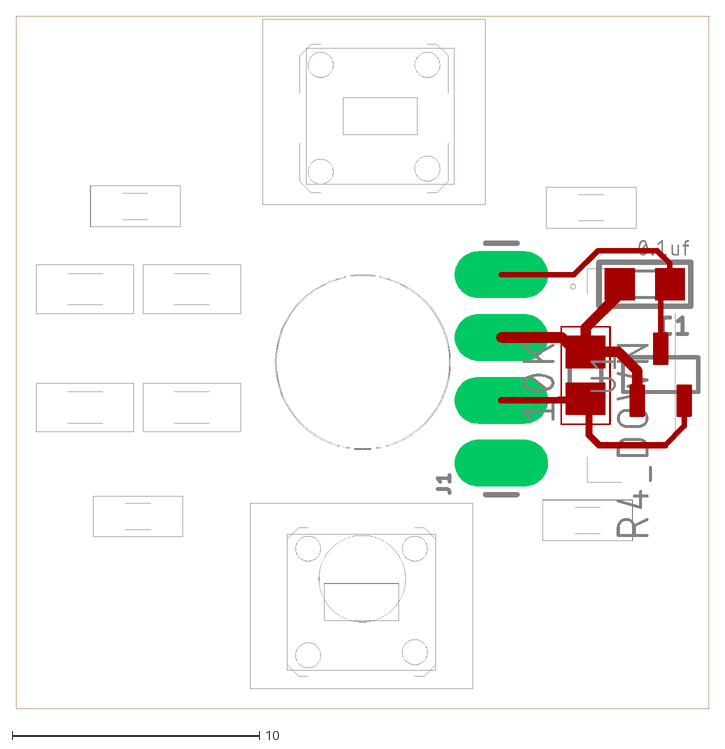
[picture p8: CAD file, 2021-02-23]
Hardware/Circuits/PCB/MagnetAdapter.dxf
28.0 x 28.0

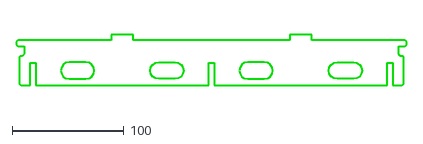
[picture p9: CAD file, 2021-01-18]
Hardware/Desgins/module_2_smt.dxf
350.3 x 45.0

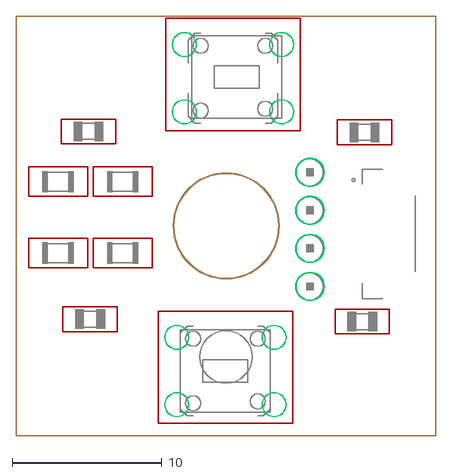
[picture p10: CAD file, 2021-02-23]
Hardware/Circuits/PCB/LEDBox.dxf
28.0 x 28.0

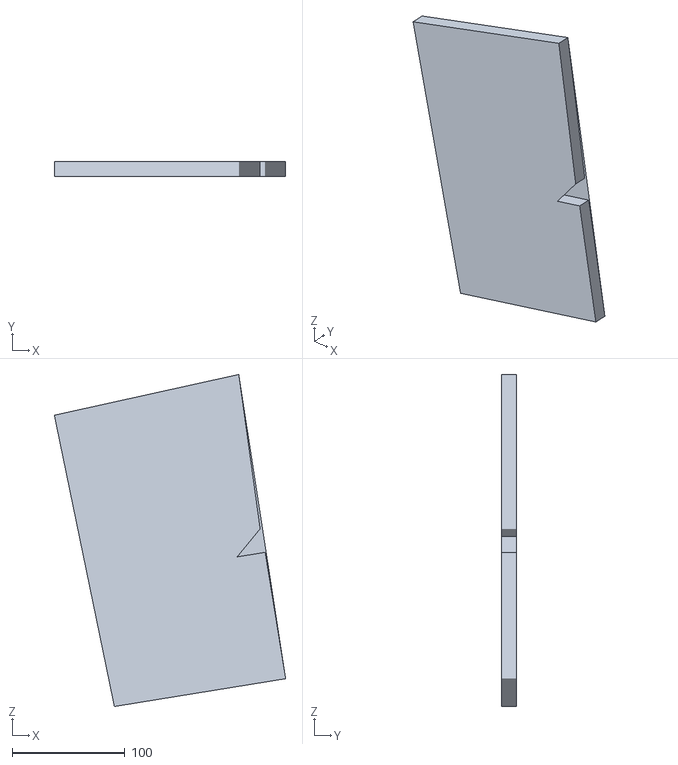
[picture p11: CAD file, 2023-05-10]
Code/InterfaceApp/VolpeExperienceLight/data/G0.obj
205.0 x 13.0 x 294.2

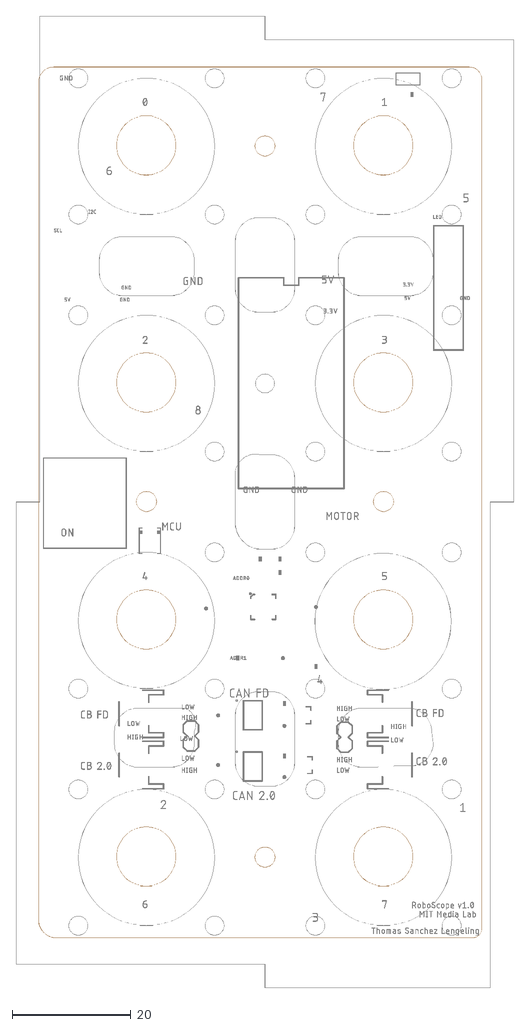
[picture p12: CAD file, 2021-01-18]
Hardware/Circuits/PCB/MotorControl_M.dxf
84.0 x 164.0

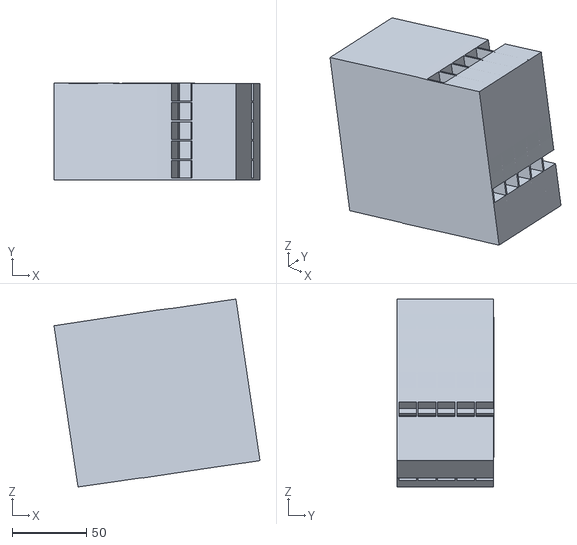
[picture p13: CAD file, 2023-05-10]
Code/InterfaceApp/VolpeExperienceLight/data/A1.obj
138.6 x 65.1 x 126.5

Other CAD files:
Code/InterfaceApp/VolpeExperienceLight/data/A9.obj
Hardware/Desgins/BASE_8X2.dwg
Hardware/Desgins/module_2_smb.dxf
Hardware/Desgins/2x2 Base Supports 200921.dxf
Code/InterfaceApp/VolpeExperienceLight/data/A2.obj
Hardware/Desgins/4X4TOP.dxf
Code/InterfaceApp/VolpeExperienceLight/data/A12.obj
Hardware/Desgins/base_module.dxf
Code/InterfaceApp/VolpeExperienceLight/data/A10.obj
Hardware/Desgins/module_2.dxf.dwg
Code/InterfaceApp/VolpeExperienceLight/data/A11.obj
Code/InterfaceApp/VolpeExperienceLight/data/A3.obj
Code/InterfaceApp/VolpeExperienceLight/data/A4.obj
Code/InterfaceApp/VolpeExperienceLight/data/A5.obj
Code/InterfaceApp/VolpeExperienceLight/data/A6.obj
Code/InterfaceApp/VolpeExperienceLight/data/A7.obj
Code/InterfaceApp/VolpeExperienceLight/data/G1.obj
Code/InterfaceApp/VolpeExperienceLight/data/volpe_base.obj
Code/InterfaceApp/VolpeExperienceLight/data/volpe_noBase.obj
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

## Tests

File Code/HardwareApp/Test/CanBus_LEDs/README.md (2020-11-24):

# CanBus + Interaction Board LEDs Test Code 

This code tests the serial and CAN bus communication pipeline from the CS CityScope Interface App to the Interaction Board of the table

## Server

-  Combination of serial communication code and CAN bus messaging 
-  Will send data received from Digital Controls to connected clients through CAN bus msgs
    + One CAN bus msg per node
        * ID: node ID
        * Buffer: [height, interaction, color1, color2] x8
- Will send data received from clients to Digital Controls through serial communication
    + Char array in the form:
        * "nodeID,height,interaction,color1,color2,height..."
- Serial Input Tests:
    + a: turn neopixels white
    + b: turn neopixels blue
    + c,{int 0-255},{int 0-255}: turn neopixels into given rgb565 color
    + Example Interface inputs to use:
        * W0,0,20,224,195,1,8,27,214,2,20,224,195,3,8,27,214,4,20,224,195,5,20,224,195,6,8,105,243,7,8,105,243E
        * W0,0,8,252,211,1,20,224,195,2,8,27,214,3,8,27,214,4,8,27,214,5,8,27,214,6,8,105,243,7,8,105,243E
    
## CANFD_Client
-  Will read and process data from CANFD_Server
-  Displays information through colors on NeoPixels

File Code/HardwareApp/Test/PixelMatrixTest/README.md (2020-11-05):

# Pixel Matrix Test Code 

This code tests the serial and CAN bus communication pipeline from the CS CityScope Interface App to a Pixel Matrix (substitute for the RoboScope table)

## Translator.ino

-  The first iteration of Translator code and only has serial communication code
-  Information is sent pixel by pixel 
-  Features: button input to send defined data to interface app as a test

## Server 

-  Combination of serial communication code and CAN bus messaging 
-  Will send data received from Digital Controls to connected clients through CAN bus msgs
    + One CAN bus msg per node
        * ID: node ID
        * Buffer: [height, interaction, color1, color2] x8
- Will send data received from clients to Digital Controls through serial communication
    + Char array in the form:
        * "nodeID,height,interaction,color1,color2,height..."
    
## Client

-  Will read and process data from CANFD_Server
-  Displays information on pixel matrix using SmartMatrix3 library
-  Sends back CANbus msg (on serial input) to test Digital Controls receiving capabilities

For more information about the CANFD Server and Client, see the  check out the [CANBUS Test folder](https://github.com/CityScope/CS_RoboScope/tree/master/Code/HardwareApp/Test/CanBus/CAN_BUS_FD_2.0).

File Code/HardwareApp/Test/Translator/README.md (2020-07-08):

## READ ME

The servoBoardTest.ino script is meant to be used as a tester script for the ClientBoard script. It tests the CAN Bus communication and message interpretation for the ClientBoard.

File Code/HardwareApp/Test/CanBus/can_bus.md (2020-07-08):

Simple CAN interface
http://henrysbench.capnfatz.com/henrys-bench/arduino-projects-tips-and-more/build-an-arduino-can-transceiver/

Teensy CAN BUS:

CAN BUS eagle:
https://github.com/dmavromatis/mavroOBD/

https://www.seeedstudio.com/Serial-CAN-BUS-Module-based-on-MCP2551-and-MCP2515.html

http://www.industrialberry.com/canberry-v-2-0/

https://harrisonsand.com/static/CAN_module.pdf

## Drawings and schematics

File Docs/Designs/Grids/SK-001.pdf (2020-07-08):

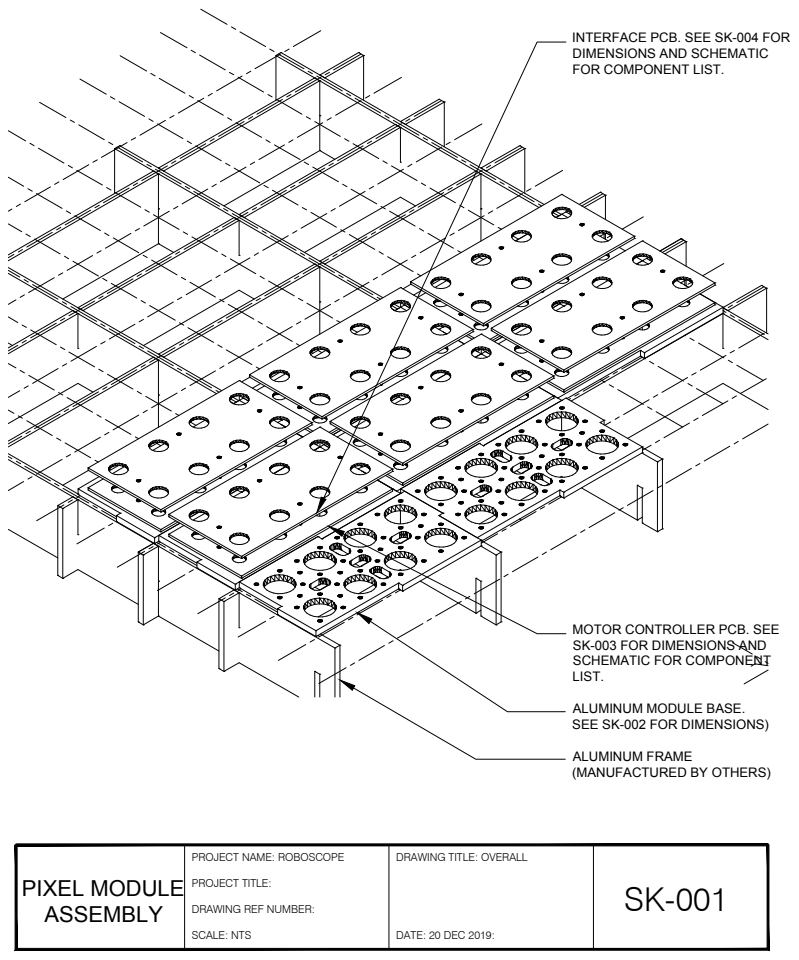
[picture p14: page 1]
PROJECT TITLE:; SCALE: NTS; DATE: 20 DEC 2019:

INTERFACE PCB. SEE SK-004 FOR
DIMENSIONS AND SCHEMATIC
FOR COMPONENT LIST.

MOTOR CONTROLLER PCB. SEE
SK-003 FOR DIMENSIONS AND
SCHEMATIC FOR COMPONENT
LIST.

ALUMINUM MODULE BASE.
SEE SK-002 FOR DIMENSIONS)

ALUMINUM FRAME
(MANUFACTURED BY OTHERS)

PROJECT NAME: ROBOSCOPE

DRAWING TITLE: OVERALL

SK-001 PIXEL MODULE
ASSEMBLY

DRAWING REF NUMBER:

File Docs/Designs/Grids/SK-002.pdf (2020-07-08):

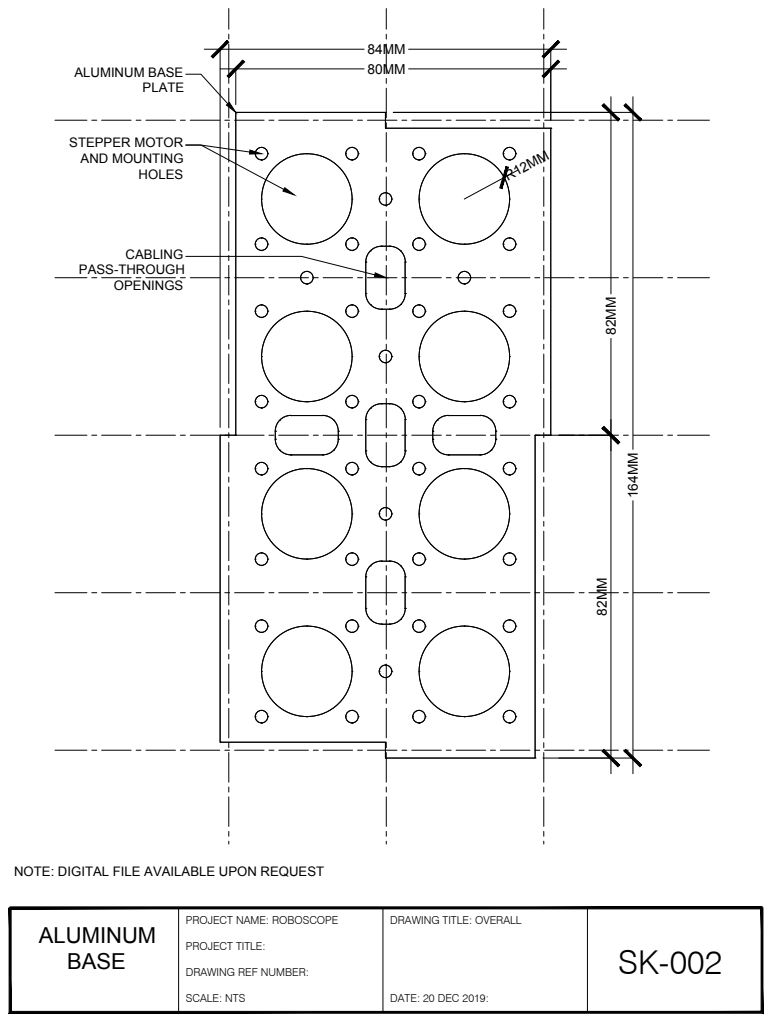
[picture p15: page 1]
STEPPER MOTOR AND MOUNTING; ALUMINUM BASE; PROJECT TITLE:; SCALE: NTS; DATE: 20 DEC 2019:

NOTE: DIGITAL FILE AVAILABLE UPON REQUEST

PROJECT NAME: ROBOSCOPE

DRAWING TITLE: OVERALL

DRAWING REF NUMBER:

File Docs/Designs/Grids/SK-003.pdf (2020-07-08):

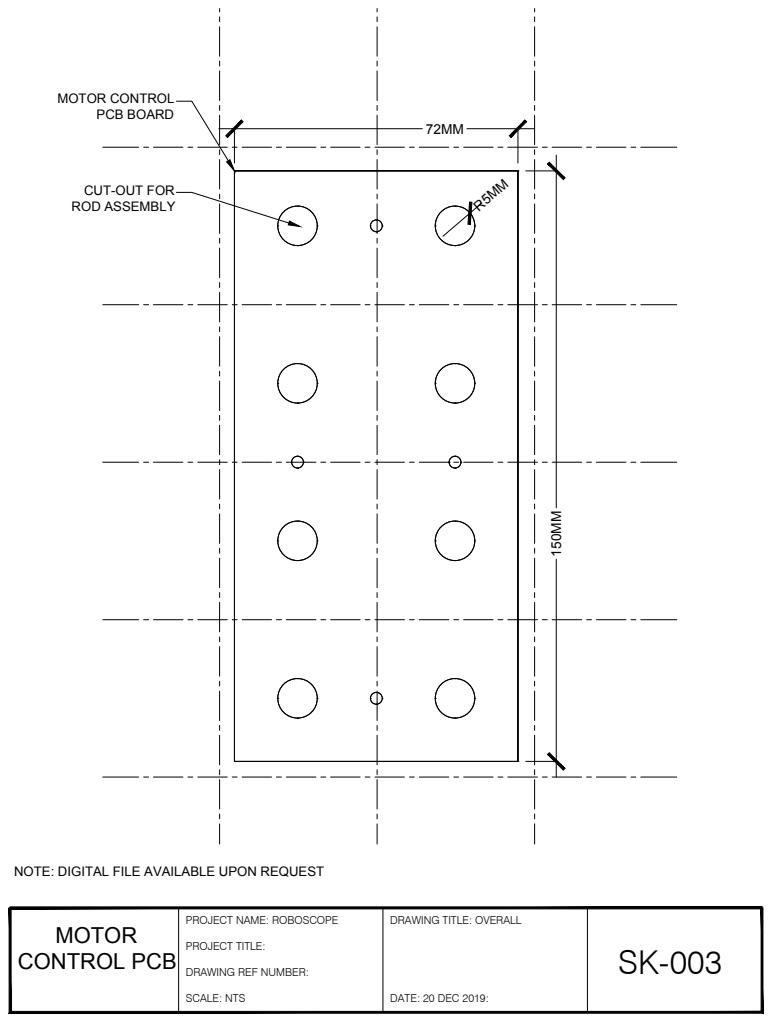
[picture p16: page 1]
MOTOR CONTROL PCB BOARD; ROD ASSEMBLY; PROJECT TITLE:; SCALE: NTS; DATE: 20 DEC 2019:; CONTROL PCB

CUT-OUT FOR

NOTE: DIGITAL FILE AVAILABLE UPON REQUEST

PROJECT NAME: ROBOSCOPE

DRAWING TITLE: OVERALL

DRAWING REF NUMBER:

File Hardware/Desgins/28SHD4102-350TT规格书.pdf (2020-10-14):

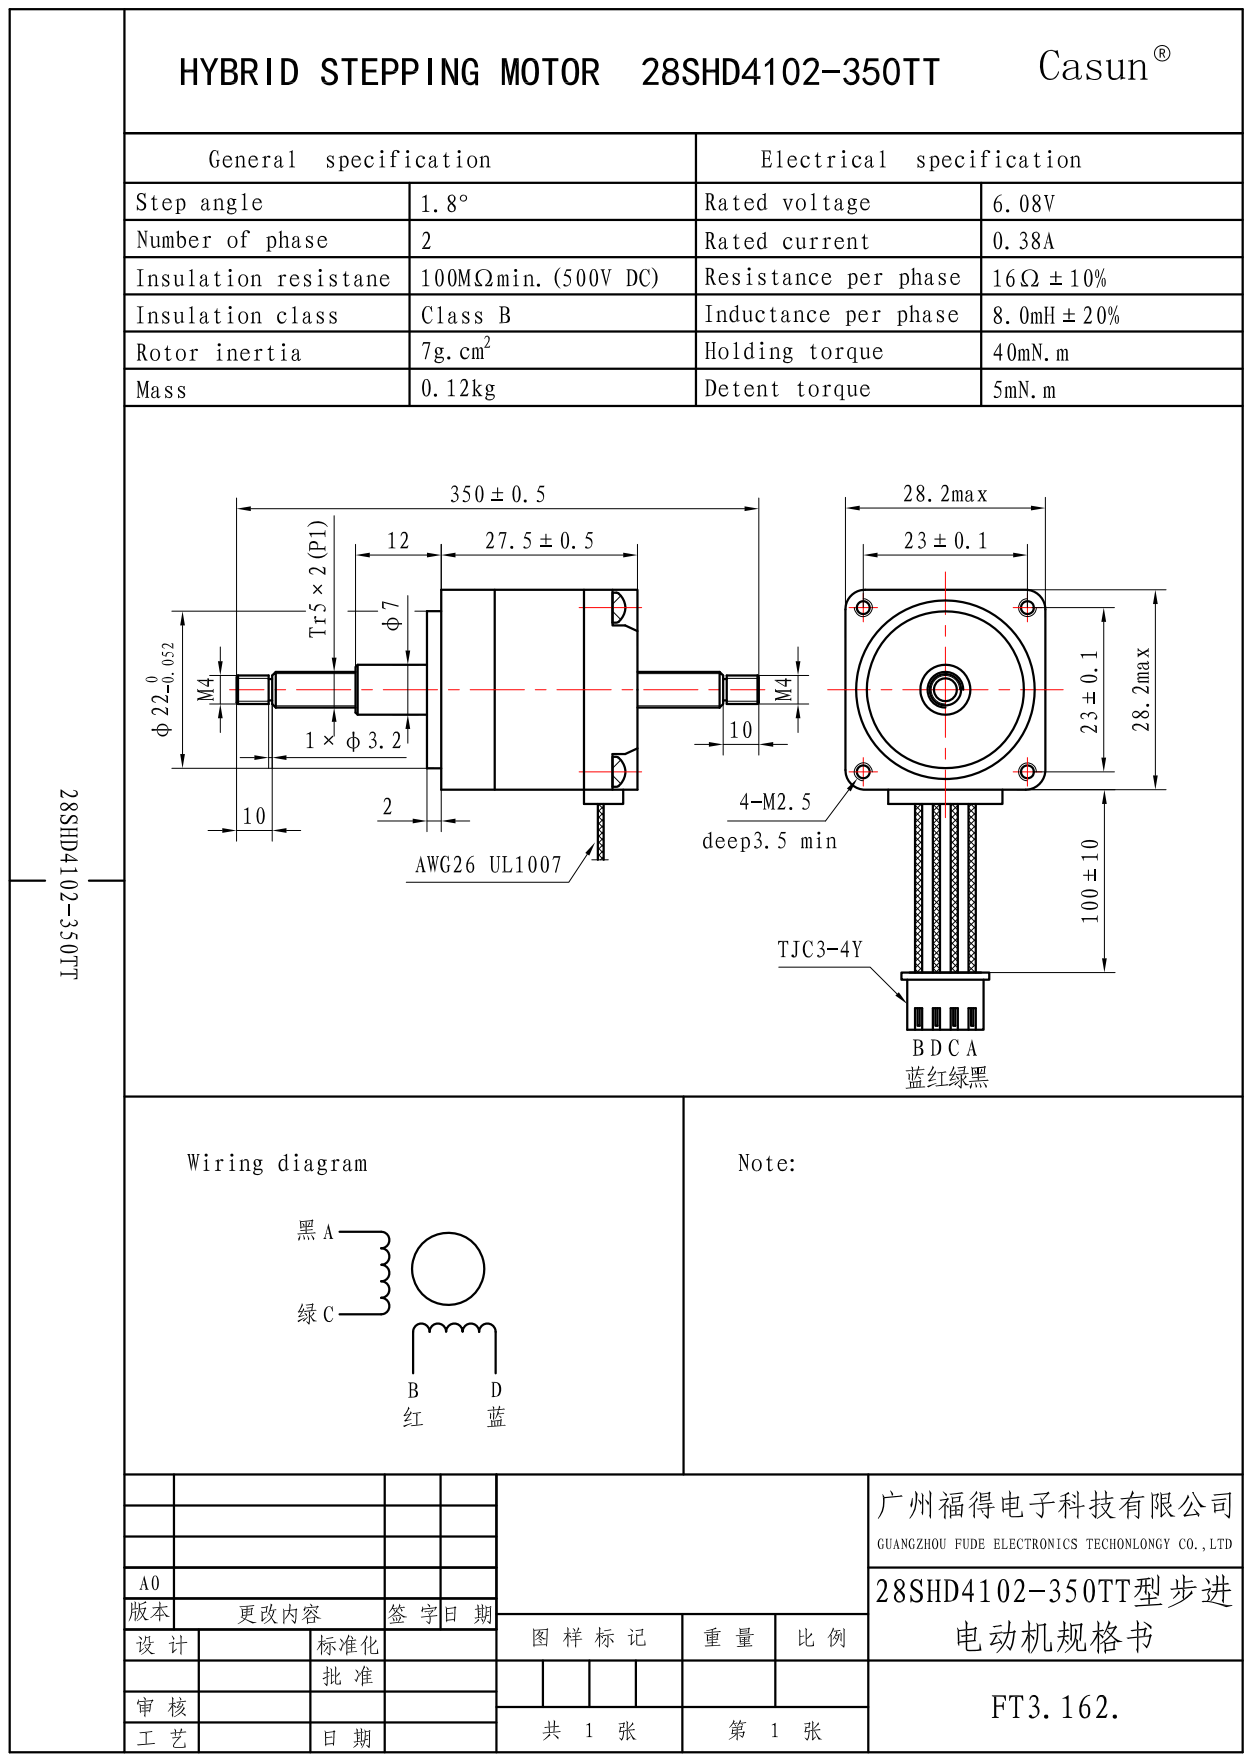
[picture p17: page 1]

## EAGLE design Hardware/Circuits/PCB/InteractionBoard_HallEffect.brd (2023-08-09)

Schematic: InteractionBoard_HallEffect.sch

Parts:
C1, C2, C3, C4, C5, C6, C7, C8, C9, C12, C13, C14, C15, C16, C17, C18, C19: 0.1uF; 0603-CAP
J3: F-2X10-DIL-2MM; DIL-2MM-2X10
JP1: JUMPER-SMT_3_1-NC_TRACE_NO-SILK; SMT-JUMPER_3_1-NC_TRACE_NO-SILK
JP6, JP7, JP8, JP9, JP10, JP11: JUMPER-SMT_2_NC_TRACE_NO-SILK; SMT-JUMPER_2_NC_TRACE_NO-SILK
M_01, M_02, M_03, M_04, M_05, M_06, M_07, M_08: CONN_06SMD-1MM; 1X06-1MM
POWER_3.3: LEDFAB1206; LED1206FAB
R9, R10, R11, R12, R13, R14, R16, R17, R18, R19, R20, R21, R23, R24, R25, R26: 10K; 0603-RES
R27, R28: 500; 0603-RES
RN1, RN2, RN3: 4R-NEXB38V; EXB38V
S1: JS207011SCQNR; SW_JS207011SCQNR
S2: MOMENTARY-SWITCH-SPST-2-SMD-5.2MM; TACTILE_SWITCH_SMD_5.2MM
STATUS: LEDFAB1206; LED1206FAB
SW1: 219-10; CTS-219-10
SX1509_2, SX1509_3: SX1509; QFN-28
U1, U3, U4, U5, U6, U7, U8, U9: DRV5032FADBZRDBZ0003A_L; DBZ0003A_L
U2: SX1509; QFN-28

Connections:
0_SX1: M_04.6, SX1509_2.27 (I/O[0])
0_SX2: M_08.6, U2.27 (I/O[0])
0_SX3: SX1509_3.27 (I/O[0])
1_SX1: M_04.5, SX1509_2.28 (I/O[1])
1_SX2: M_08.5, U2.28 (I/O[1])
1_SX3: J3.16, SX1509_3.28 (I/O[1])
2_SX1: M_02.6, SX1509_2.1 (I/O[2])
2_SX2: M_06.6, U2.1 (I/O[2])
2_SX3: SX1509_3.1 (I/O[2])
3.3V: C1.1, C2.1, C3.1, C4.1, C5.1, C6.1, C7.1, C8.1, C9.1, C12.1, C13.1, C14.1, C15.1, C16.1, C17.1, C18.1, C19.1, J3.19, R9.2, R10.2, R11.2, R12.2, R13.2, R14.2, R16.2, R17.2, R18.2, R19.2, R20.2, R21.2, R23.2, R24.2, R25.2, R26.2, R27.2, RN1.5 (2), RN1.6 (2), RN1.7 (2), RN1.8 (2), RN2.7 (2), RN2.8 (2), RN3.5 (2), RN3.6 (2), RN3.7 (2), RN3.8 (2), S2.1, S2.2, SX1509_2.4 (VCC1), SX1509_2.12 (VDDM), SX1509_2.18 (VCC2), SX1509_3.4 (VCC1), SX1509_3.12 (VDDM), SX1509_3.18 (VCC2), U1.1 (VCC), U2.4 (VCC1), U2.12 (VDDM), U2.18 (VCC2), U3.1 (VCC), U4.1 (VCC), U5.1 (VCC), U6.1 (VCC), U7.1 (VCC), U8.1 (VCC), U9.1 (VCC)
3_SX1: M_02.5, SX1509_2.2 (I/O[3])
3_SX2: M_06.5, U2.2 (I/O[3])
3_SX3: J3.12, SX1509_3.2 (I/O[3])
4_SX1: M_02.4, SX1509_2.5 (I/O[4])
4_SX2: M_06.4, U2.5 (I/O[4])
4_SX3: JP1.1, SX1509_3.5 (I/O[4])
5_SX1: M_04.4, SX1509_2.6 (I/O[5])
5_SX2: M_08.4, U2.6 (I/O[5])
5_SX3: R28.2, SX1509_3.6 (I/O[5])
6_SX1: SX1509_2.7 (I/O[6]), U3.2 (OUT)
6_SX2: U2.7 (I/O[6]), U7.2 (OUT)
6_SX3: RN1.1, SW1.20, SX1509_3.7 (I/O[6])
7_SX1: SX1509_2.8 (I/O[7]), U5.2 (OUT)
7_SX2: U2.8 (I/O[7]), U9.2 (OUT)
7_SX3: RN1.2 (1), SW1.19, SX1509_3.8 (I/O[7])
8_SX1: SX1509_2.13 (I/O[8]), U1.2 (OUT)
8_SX2: U2.13 (I/O[8]), U6.2 (OUT)
8_SX3: RN1.3 (1), SW1.18, SX1509_3.13 (I/O[8])
9_SX1: SX1509_2.14 (I/O[9]), U4.2 (OUT)
9_SX2: U2.14 (I/O[9]), U8.2 (OUT)
9_SX3: RN1.4 (1), SW1.17, SX1509_3.14 (I/O[9])
10_SX1: M_01.6, SX1509_2.15 (I/O[10])
10_SX2: M_05.6, U2.15 (I/O[10])
10_SX3: RN3.1, SW1.16, SX1509_3.15 (I/O[10])
11_SX1: M_01.5, SX1509_2.16 (I/O[11])
11_SX2: M_05.5, U2.16 (I/O[11])
11_SX3: RN3.2 (1), SW1.15, SX1509_3.16 (I/O[11])
12_SX1: M_01.4, SX1509_2.19 (I/O[12])
12_SX2: M_05.4, U2.19 (I/O[12])
12_SX3: RN3.3 (1), SW1.14, SX1509_3.19 (I/O[12])
13_SX1: M_03.6, SX1509_2.20 (I/O[13])
13_SX2: M_07.6, U2.20 (I/O[13])
13_SX3: RN3.4 (1), SW1.13, SX1509_3.20 (I/O[13])
14_SX1: M_03.5, SX1509_2.21 (I/O[14])
14_SX2: M_07.5, U2.21 (I/O[14])
14_SX3: RN2.1, SW1.12, SX1509_3.21 (I/O[14])
15_SX1: M_03.4, SX1509_2.22 (I/O[15])
15_SX2: M_07.4, U2.22 (I/O[15])
15_SX3: RN2.2 (1), SW1.11, SX1509_3.22 (I/O[15])
!RESET_SX1: R9.1, SX1509_2.23 (!RESET)
!RESET_SX2: R16.1, U2.23 (!RESET)
!RESET_SX3: R14.1, SX1509_3.23 (!RESET)
ADDR0_SX1: JP8.1, SX1509_2.26 (ADDR0)
ADDR0_SX2: JP7.1, U2.26 (ADDR0)
ADDR0_SX3: JP11.1, SX1509_3.26 (ADDR0)
ADDR1_SX1: JP9.1, SX1509_2.10 (ADDR1)
ADDR1_SX2: JP6.1, U2.10 (ADDR1)
ADDR1_SX3: JP10.1, SX1509_3.10 (ADDR1)
GND_MCU: C1.2, C2.2, C3.2, C4.2, C5.2, C6.2, C7.2, C8.2, C9.2, C12.2, C13.2, C14.2, C15.2, C16.2, C17.2, C18.2, C19.2, J3.18, J3.20, JP7.2, JP9.2, M_01.1, M_02.1, M_03.1, M_04.1, M_05.1, M_06.1, M_07.1, M_08.1, POWER_3.3.2 (C), RN2.3 (1), STATUS.2 (C), SW1.1, SW1.2, SW1.3, SW1.4, SW1.5, SW1.6, SW1.7, SW1.8, SW1.9, SW1.10, SX1509_2.3 (GND), SX1509_2.17 (GND), SX1509_2.29 (GND), SX1509_3.3 (GND), SX1509_3.17 (GND), SX1509_3.29 (GND), U1.3 (GND), U2.3 (GND), U2.17 (GND), U2.29 (GND), U3.3 (GND), U4.3 (GND), U5.3 (GND), U6.3 (GND), U7.3 (GND), U8.3 (GND), U9.3 (GND)
INT_01: J3.6, R12.1, SX1509_2.9 (!INT)
INT_02: J3.8, R19.1, U2.9 (!INT)
INT_03: J3.14, R24.1, SX1509_3.9 (!INT)
unnamed: JP6.2, R21.1
unnamed: JP8.2, R13.1
unnamed: R28.1, STATUS.1 (A)
unnamed: JP10.2, R25.1
unnamed: JP11.2, R26.1
unnamed: POWER_3.3.1 (A), R27.1
NEOPIXEL_01: J3.1, M_01.3
NEOPIXEL_02: J3.3, M_02.3
NEOPIXEL_03: J3.5, M_03.3
NEOPIXEL_04: J3.7, M_04.3
NEOPIXEL_05: J3.9, M_05.3
NEOPIXEL_06: J3.11, M_06.3
NEOPIXEL_07: J3.13, M_07.3
NEOPIXEL_08: J3.15, M_08.3
OSCIO_SX1: SX1509_2.11 (OSCIO)
OSCIO_SX2: U2.11 (OSCIO)
OSCIO_SX3: SX1509_3.11 (OSCIO)
RESET: J3.10, JP1.2, JP1.3, RN2.6 (2), S2.3, S2.4
SCL_00: J3.4, R11.1, R18.1, R23.1, SX1509_2.25 (SCL), SX1509_3.25 (SCL), U2.25 (SCL)
SDA_00: J3.2, R10.1, R17.1, R20.1, SX1509_2.24 (SDA), SX1509_3.24 (SDA), U2.24 (SDA)
VCC_5V: M_01.2, M_02.2, M_03.2, M_04.2, M_05.2, M_06.2, M_07.2, M_08.2, S1.4, S1.8
VCC_5V_IN: J3.17, S1.3, S1.7

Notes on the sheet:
INPUTS
Input power line for the BRD
I2C MUX
SWITCH
CONNECTORS
INFO
The VCC1/2 jumpers (SJ2, SJ3) set those pins to 3.3V.
I2C Address Select
VDD Range: 1.425-3.6V
Allowable VCC1/2 Range: 1.2-3.6V
IC2 MUX 01
IC2 MUX 02
IC2 MUX 03

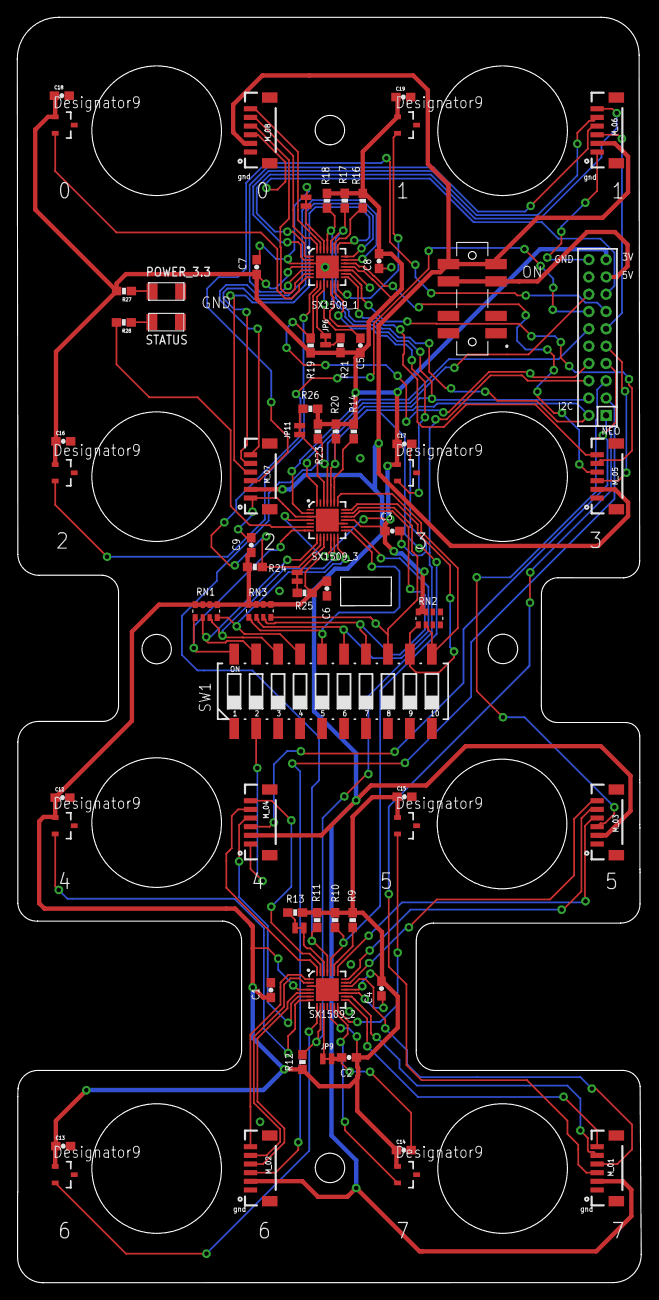
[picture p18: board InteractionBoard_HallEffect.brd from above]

Board: 2 copper layers, 72.1 x 146.3 mm, 68 parts (0 on the bottom side), 77 nets.

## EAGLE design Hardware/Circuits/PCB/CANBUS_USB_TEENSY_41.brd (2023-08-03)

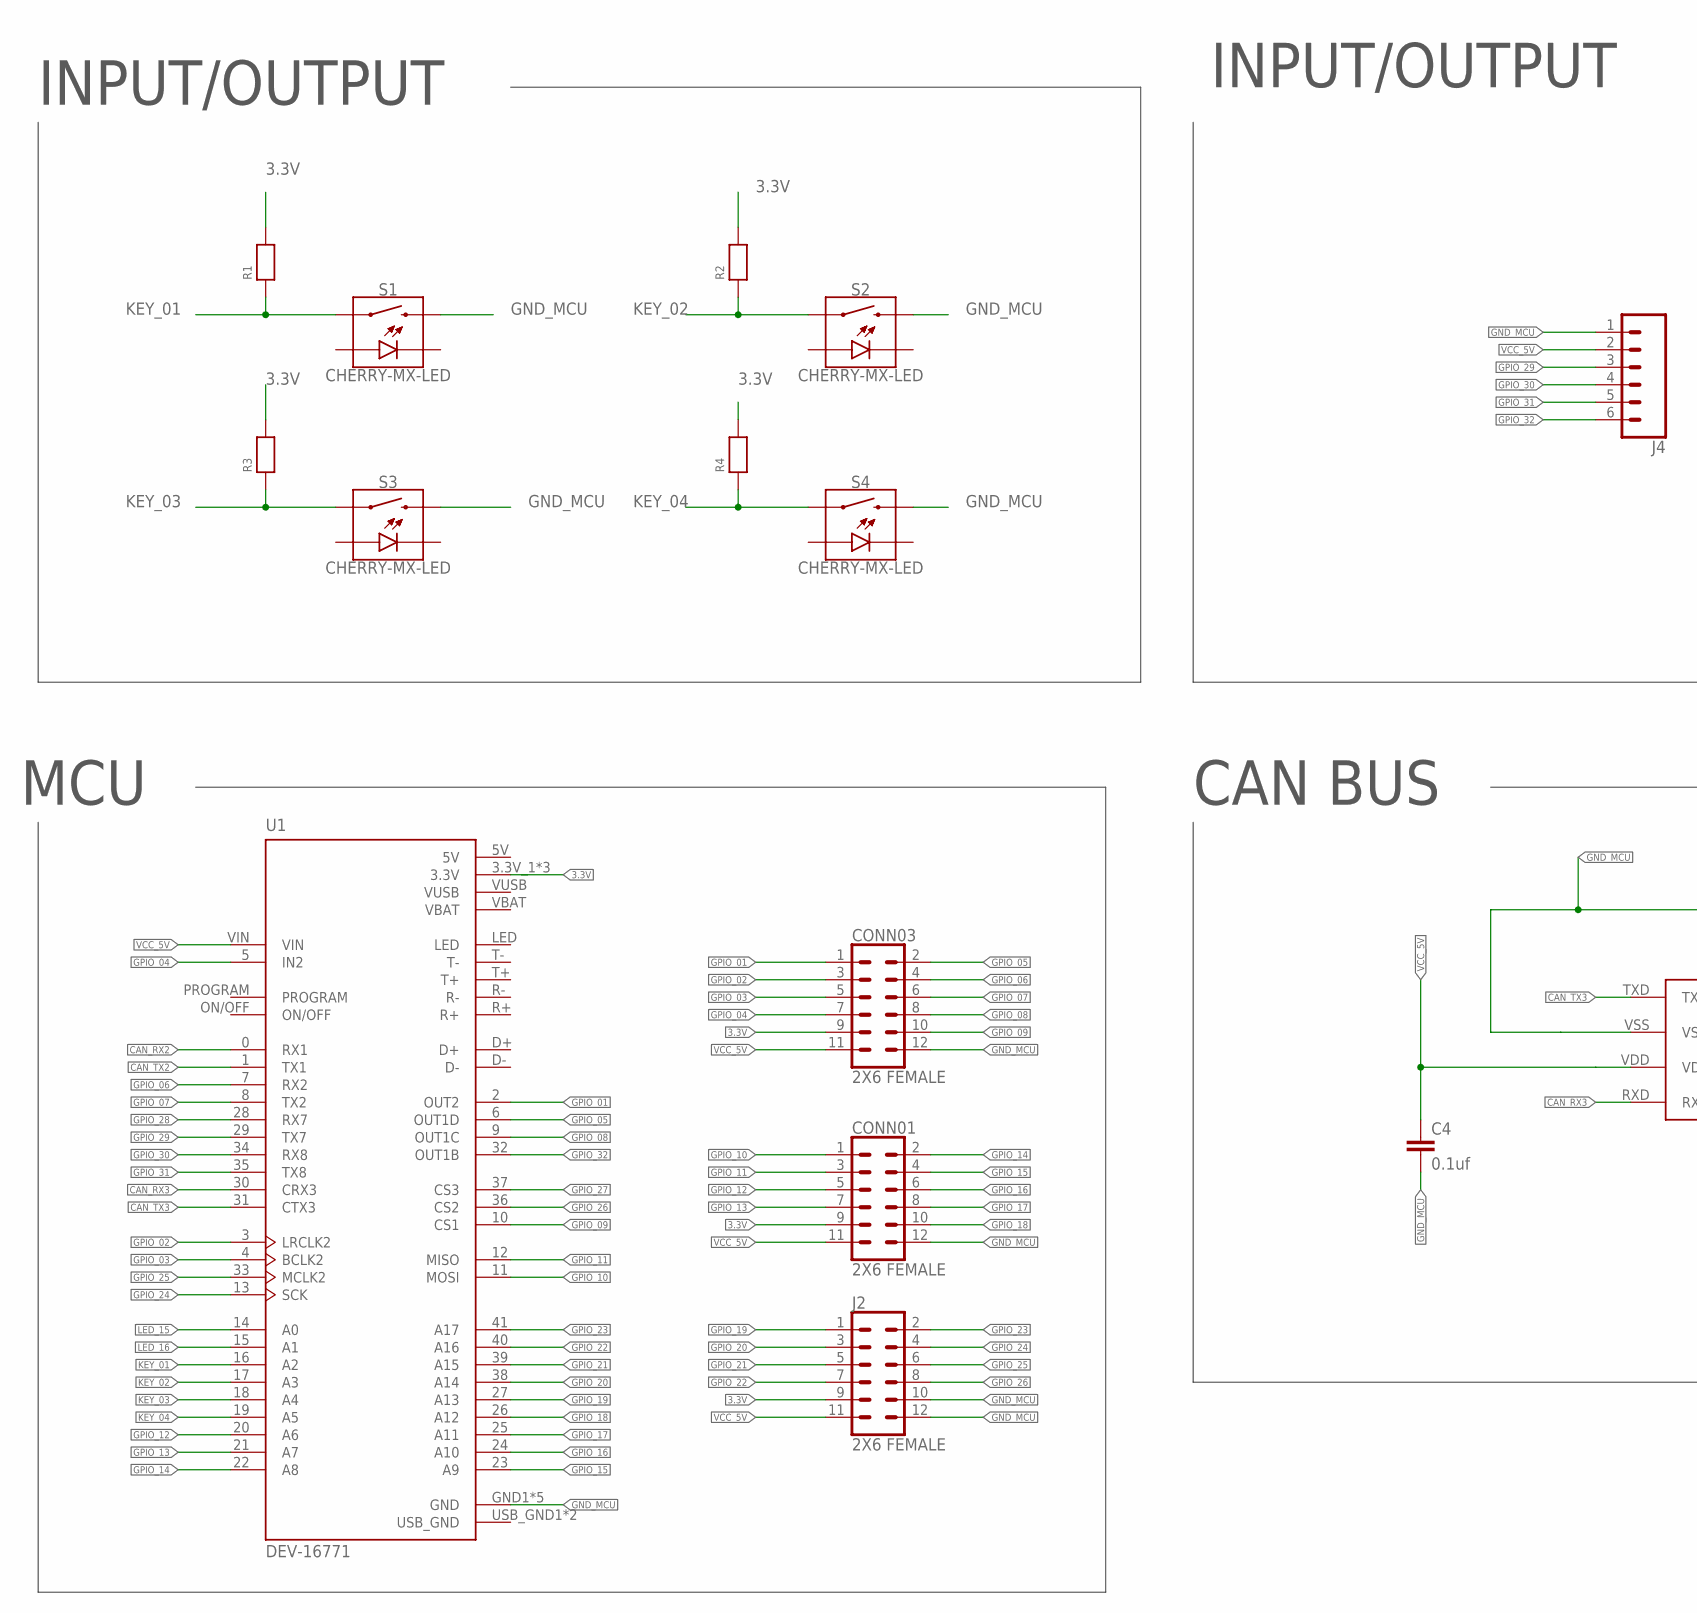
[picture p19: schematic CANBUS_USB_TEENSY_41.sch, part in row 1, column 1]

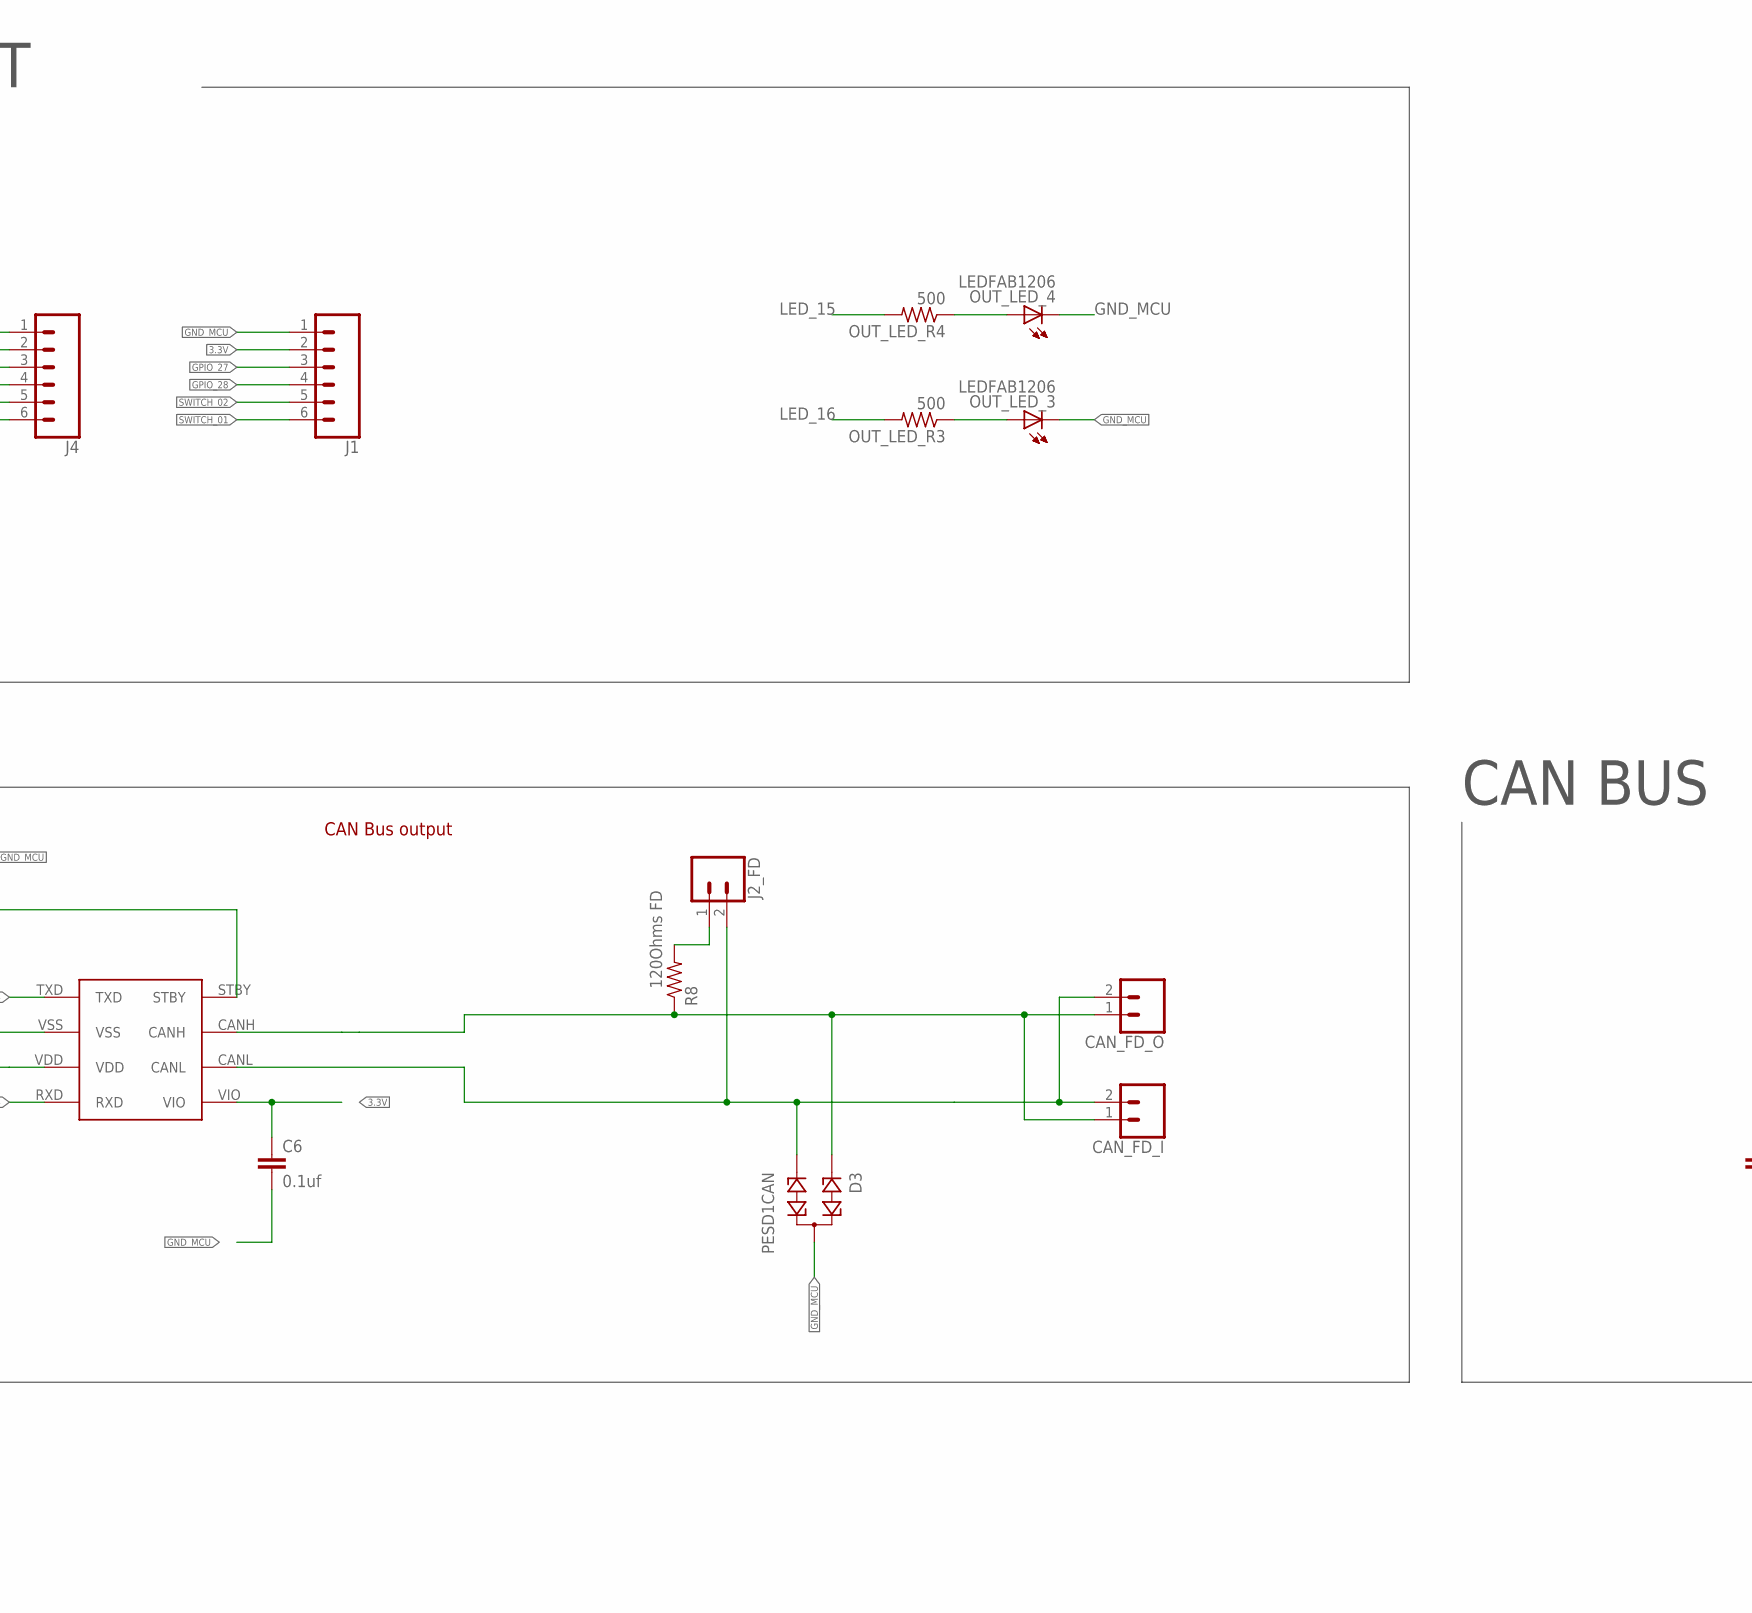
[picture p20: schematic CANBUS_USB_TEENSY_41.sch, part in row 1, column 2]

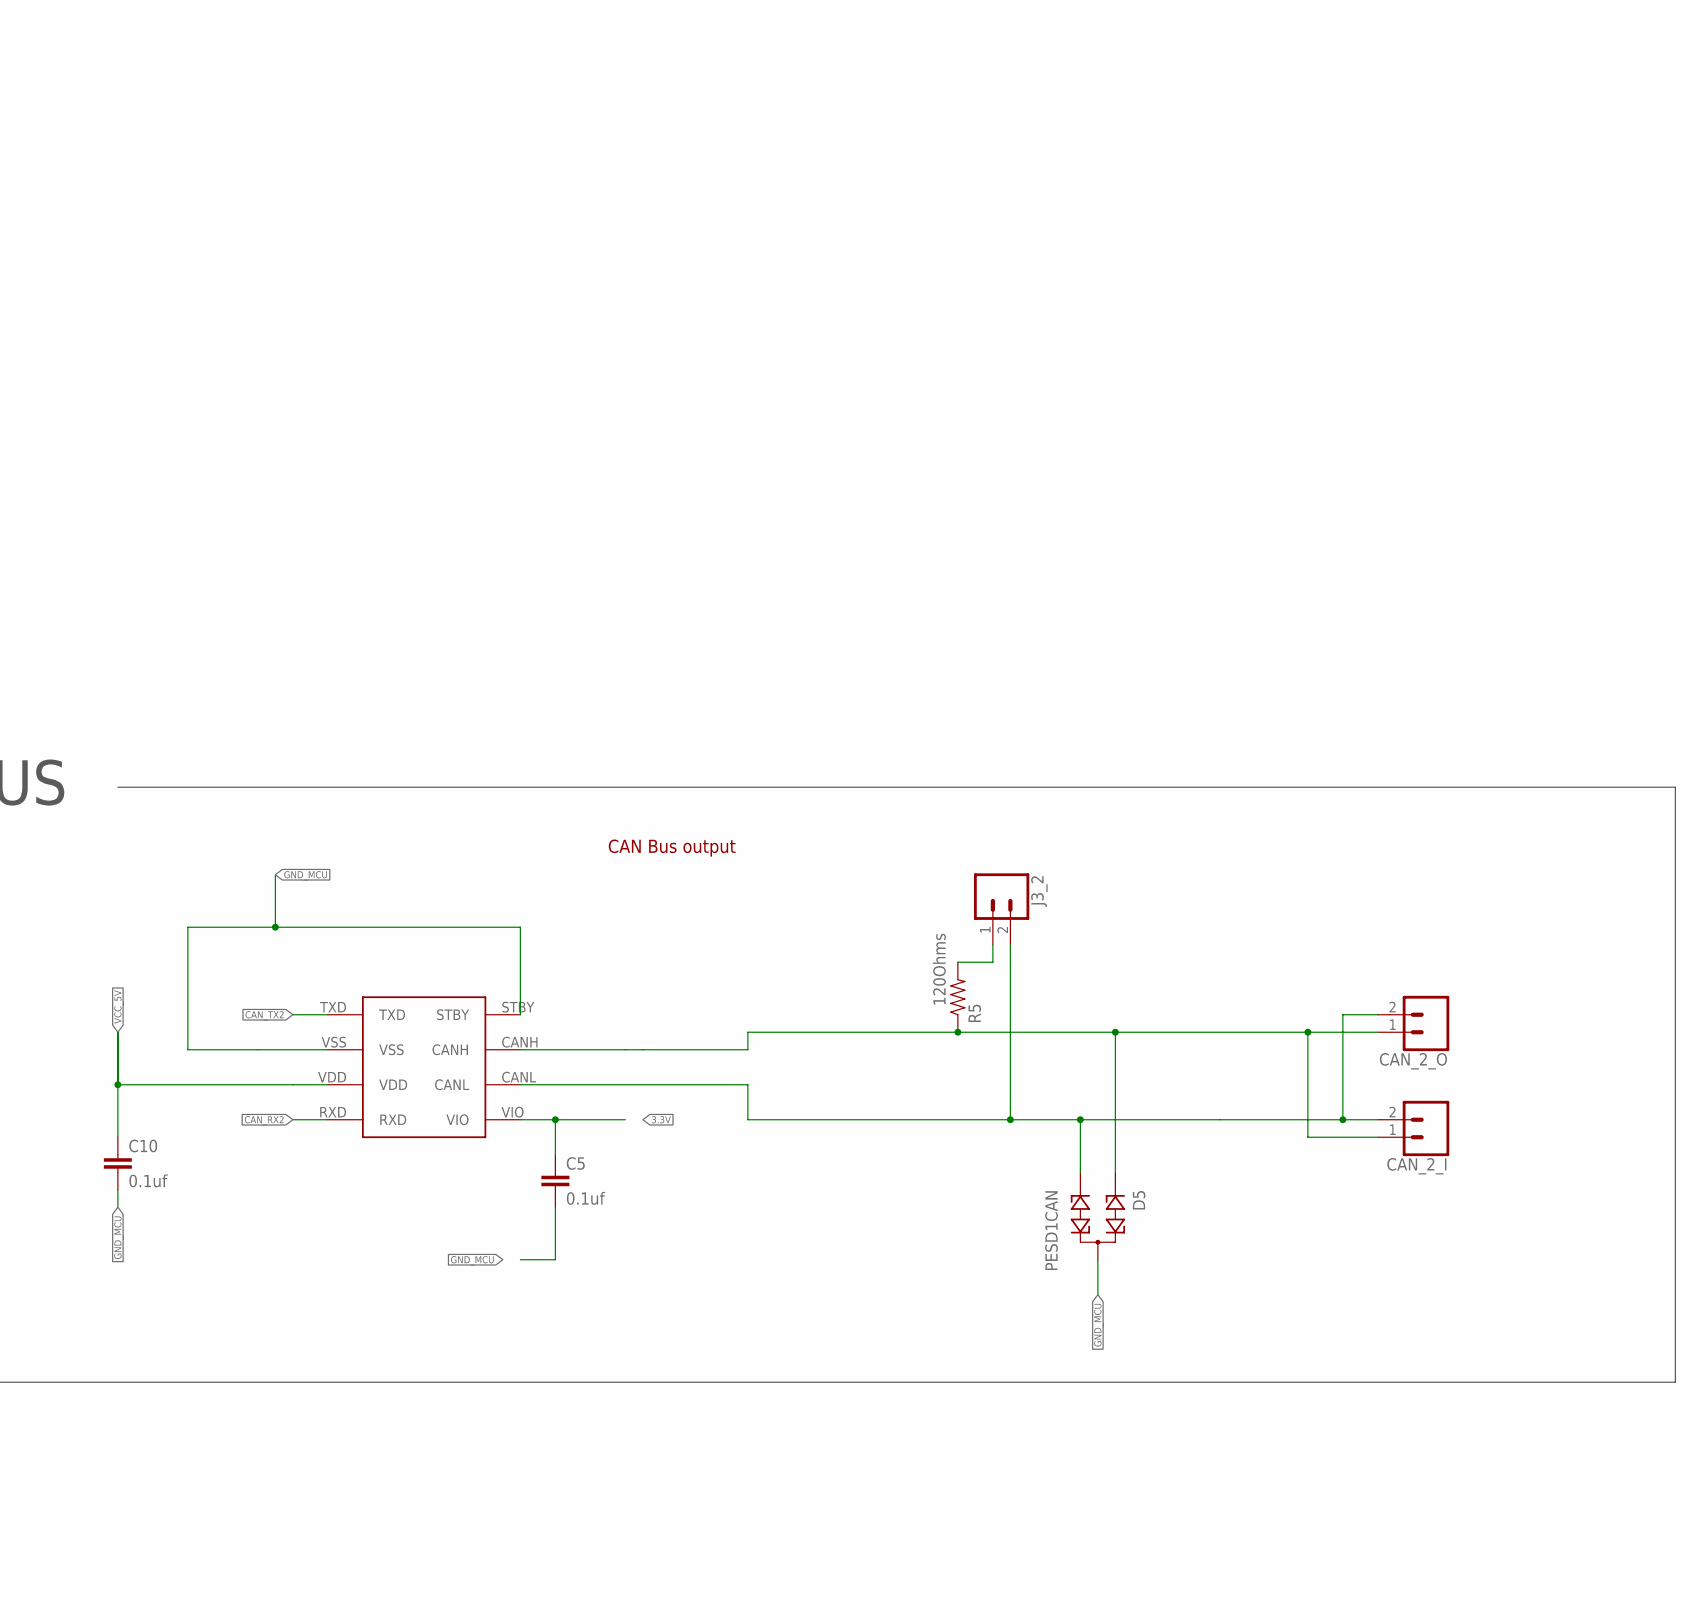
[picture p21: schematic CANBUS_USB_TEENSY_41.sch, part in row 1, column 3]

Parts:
C4, C5, C6, C10: 0.1uf; 0603-CAP
CAN_2_I, CAN_2_O: CONN_02-JST-2MM-SMT; JST-2-SMD
CAN_FD_I: CONN_02-JST-2MM-SMT; JST-2-SMD
CAN_FD_O: CONN_02-JST-2MM-SMT; JST-2-SMD
CONN01, CONN03: 2X6 FEMALE; 2X6
D3, D5: PESD1CAN; SOT23
J1, J4: CONN_06SMD-1MM; 1X06-1MM
J2: 2X6 FEMALE; 2X6
J2_FD, J3_2: CONN_02; 1X02
MCP2562, MCP2562FD: MCP2562
OUT_LED_3, OUT_LED_4: LEDFAB1206; LED1206FAB
OUT_LED_R3, OUT_LED_R4: 500; R1206FAB
R1, R2, R3, R4: RESISTOR1206; 1206
R5: 120Ohms; 0603-RES
R8: 120Ohms FD; 0603-RES
S1, S2, S3, S4: CHERRY-MX-LED
U1: DEV-16771; MODULE_DEV-16771

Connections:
3.3V: C5.1, C6.1, CONN01.9, CONN03.9, J1.2, J2.9, MCP2562.VIO, MCP2562FD.VIO, R1.2, R2.2, R3.2, R4.2, U1.3.3V_1 (3.3V), U1.3.3V_2 (3.3V), U1.3.3V_3 (3.3V)
5V: U1.5V
CAN_H: CAN_FD_I.1 (2), CAN_FD_O.1 (2), D3.1, MCP2562FD.CANH, R8.1
CAN_H1: CAN_2_I.1 (2), CAN_2_O.1 (2), D5.1, MCP2562.CANH, R5.1
CAN_L: CAN_FD_I.2 (1), CAN_FD_O.2 (1), D3.2, J2_FD.2, MCP2562FD.CANL
CAN_L1: CAN_2_I.2 (1), CAN_2_O.2 (1), D5.2, J3_2.2, MCP2562.CANL
CAN_RX2: MCP2562.RXD, U1.0 (RX1)
CAN_RX3: MCP2562FD.RXD, U1.30 (CRX3)
CAN_TX2: MCP2562.TXD, U1.1 (TX1)
CAN_TX3: MCP2562FD.TXD, U1.31 (CTX3)
GND_MCU: C4.2, C5.2, C6.2, C10.2, CONN01.12, CONN03.12, D3.3, D5.3, J1.1, J2.10, J2.12, J4.1, MCP2562.STBY, MCP2562.VSS, MCP2562FD.STBY, MCP2562FD.VSS, OUT_LED_3.2 (C), OUT_LED_4.2 (C), S1.S2, S2.S2, S3.S2, S4.S2, U1.GND1 (GND), U1.GND2 (GND), U1.GND3 (GND), U1.GND4 (GND), U1.GND5 (GND)
GPIO_01: CONN03.1, U1.2 (OUT2)
GPIO_02: CONN03.3, U1.3 (LRCLK2)
GPIO_03: CONN03.5, U1.4 (BCLK2)
GPIO_04: CONN03.7, U1.5 (IN2)
GPIO_05: CONN03.2, U1.6 (OUT1D)
GPIO_06: CONN03.4, U1.7 (RX2)
GPIO_07: CONN03.6, U1.8 (TX2)
GPIO_08: CONN03.8, U1.9 (OUT1C)
GPIO_09: CONN03.10, U1.10 (CS1)
GPIO_10: CONN01.1, U1.11 (MOSI)
GPIO_11: CONN01.3, U1.12 (MISO)
GPIO_12: CONN01.5, U1.20 (A6)
GPIO_13: CONN01.7, U1.21 (A7)
GPIO_14: CONN01.2, U1.22 (A8)
GPIO_15: CONN01.4, U1.23 (A9)
GPIO_16: CONN01.6, U1.24 (A10)
GPIO_17: CONN01.8, U1.25 (A11)
GPIO_18: CONN01.10, U1.26 (A12)
GPIO_19: J2.1, U1.27 (A13)
GPIO_20: J2.3, U1.38 (A14)
GPIO_21: J2.5, U1.39 (A15)
GPIO_22: J2.7, U1.40 (A16)
GPIO_23: J2.2, U1.41 (A17)
GPIO_24: J2.4, U1.13 (SCK)
GPIO_25: J2.6, U1.33 (MCLK2)
GPIO_26: J2.8, U1.36 (CS2)
GPIO_27: J1.3, U1.37 (CS3)
GPIO_28: J1.4, U1.28 (RX7)
GPIO_29: J4.3, U1.29 (TX7)
GPIO_30: J4.4, U1.34 (RX8)
GPIO_31: J4.5, U1.35 (TX8)
GPIO_32: J4.6, U1.32 (OUT1B)
KEY_01: R1.1, S1.S1, U1.16 (A2)
KEY_02: R2.1, S2.S1, U1.17 (A3)
KEY_03: R3.1, S3.S1, U1.18 (A4)
KEY_04: R4.1, S4.S1, U1.19 (A5)
LED_15: OUT_LED_R4.2, U1.14 (A0)
LED_16: OUT_LED_R3.2, U1.15 (A1)
unnamed: J2_FD.1, R8.2
unnamed: J3_2.1, R5.2
unnamed: OUT_LED_3.1 (A), OUT_LED_R3.1
unnamed: OUT_LED_4.1 (A), OUT_LED_R4.1
SWITCH_01: J1.6
SWITCH_02: J1.5
USB_GND: U1.USB_GND1 (USB_GND), U1.USB_GND2 (USB_GND)
VCC_5V: C4.1, C10.1, CONN01.11, CONN03.11, J2.11, J4.2, MCP2562.VDD, MCP2562FD.VDD, U1.VIN

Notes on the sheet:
MCU
INPUT/OUTPUT
CAN BUS
CAN Bus output

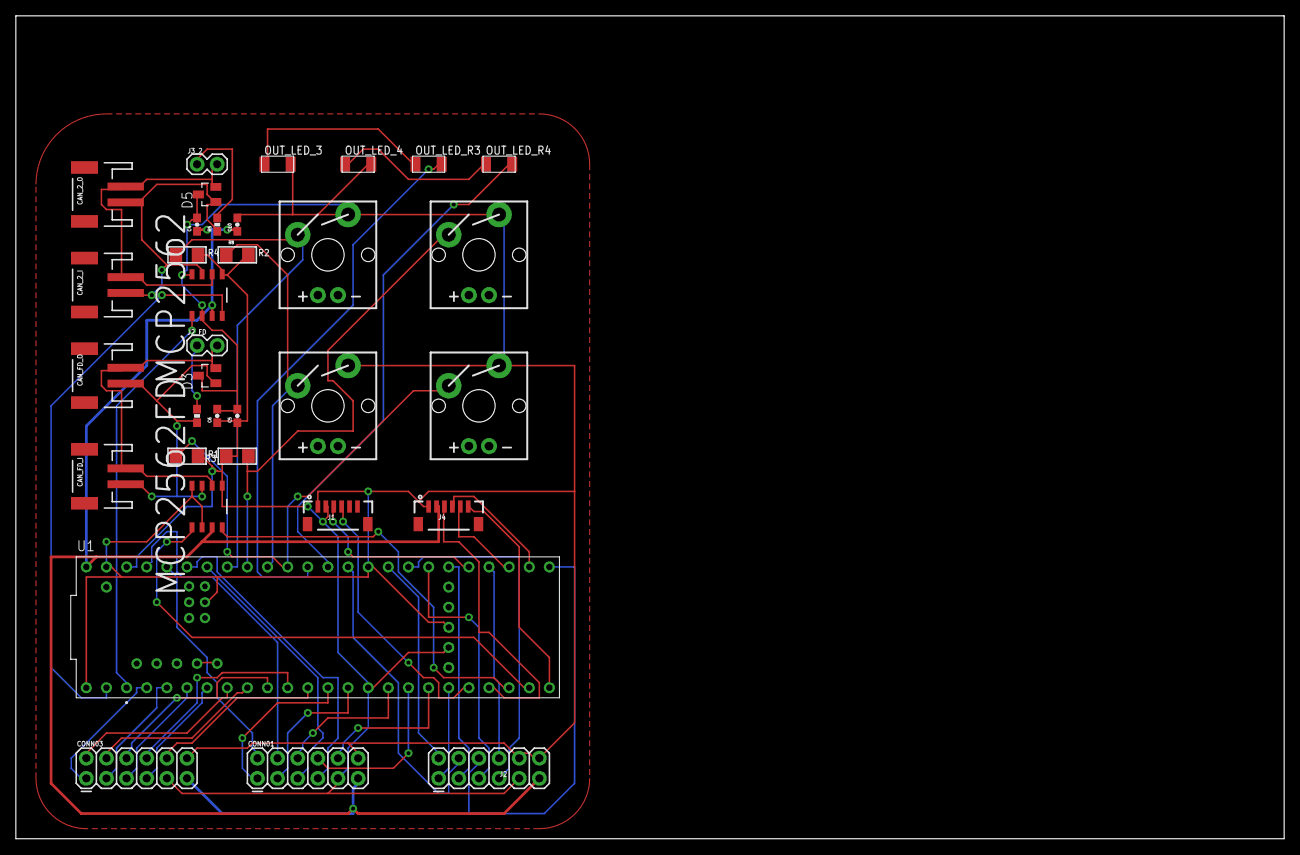
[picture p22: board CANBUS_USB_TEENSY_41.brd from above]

Board: 2 copper layers, 160.0 x 103.8 mm, 34 parts (0 on the bottom side), 54 nets.

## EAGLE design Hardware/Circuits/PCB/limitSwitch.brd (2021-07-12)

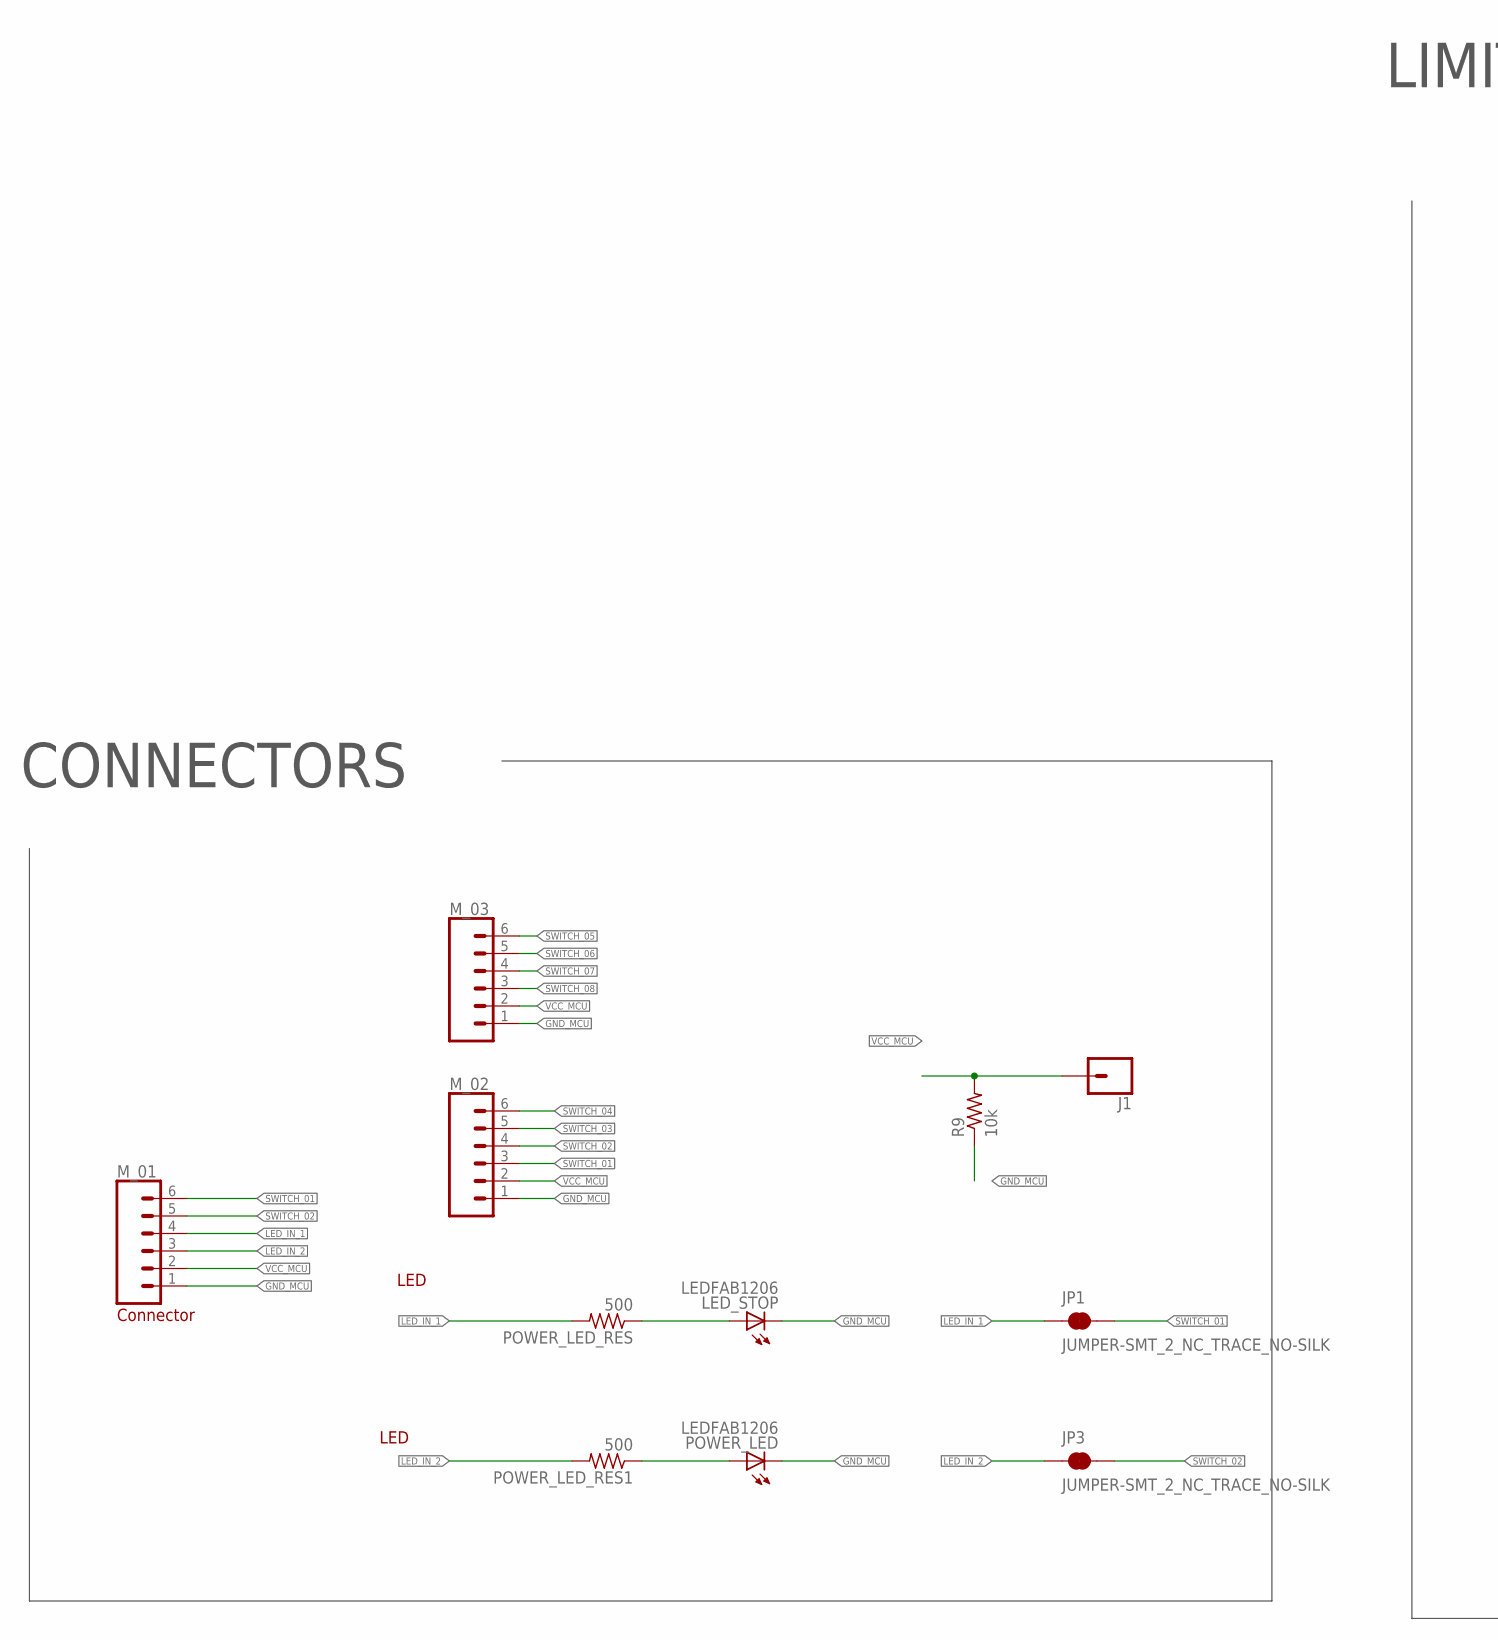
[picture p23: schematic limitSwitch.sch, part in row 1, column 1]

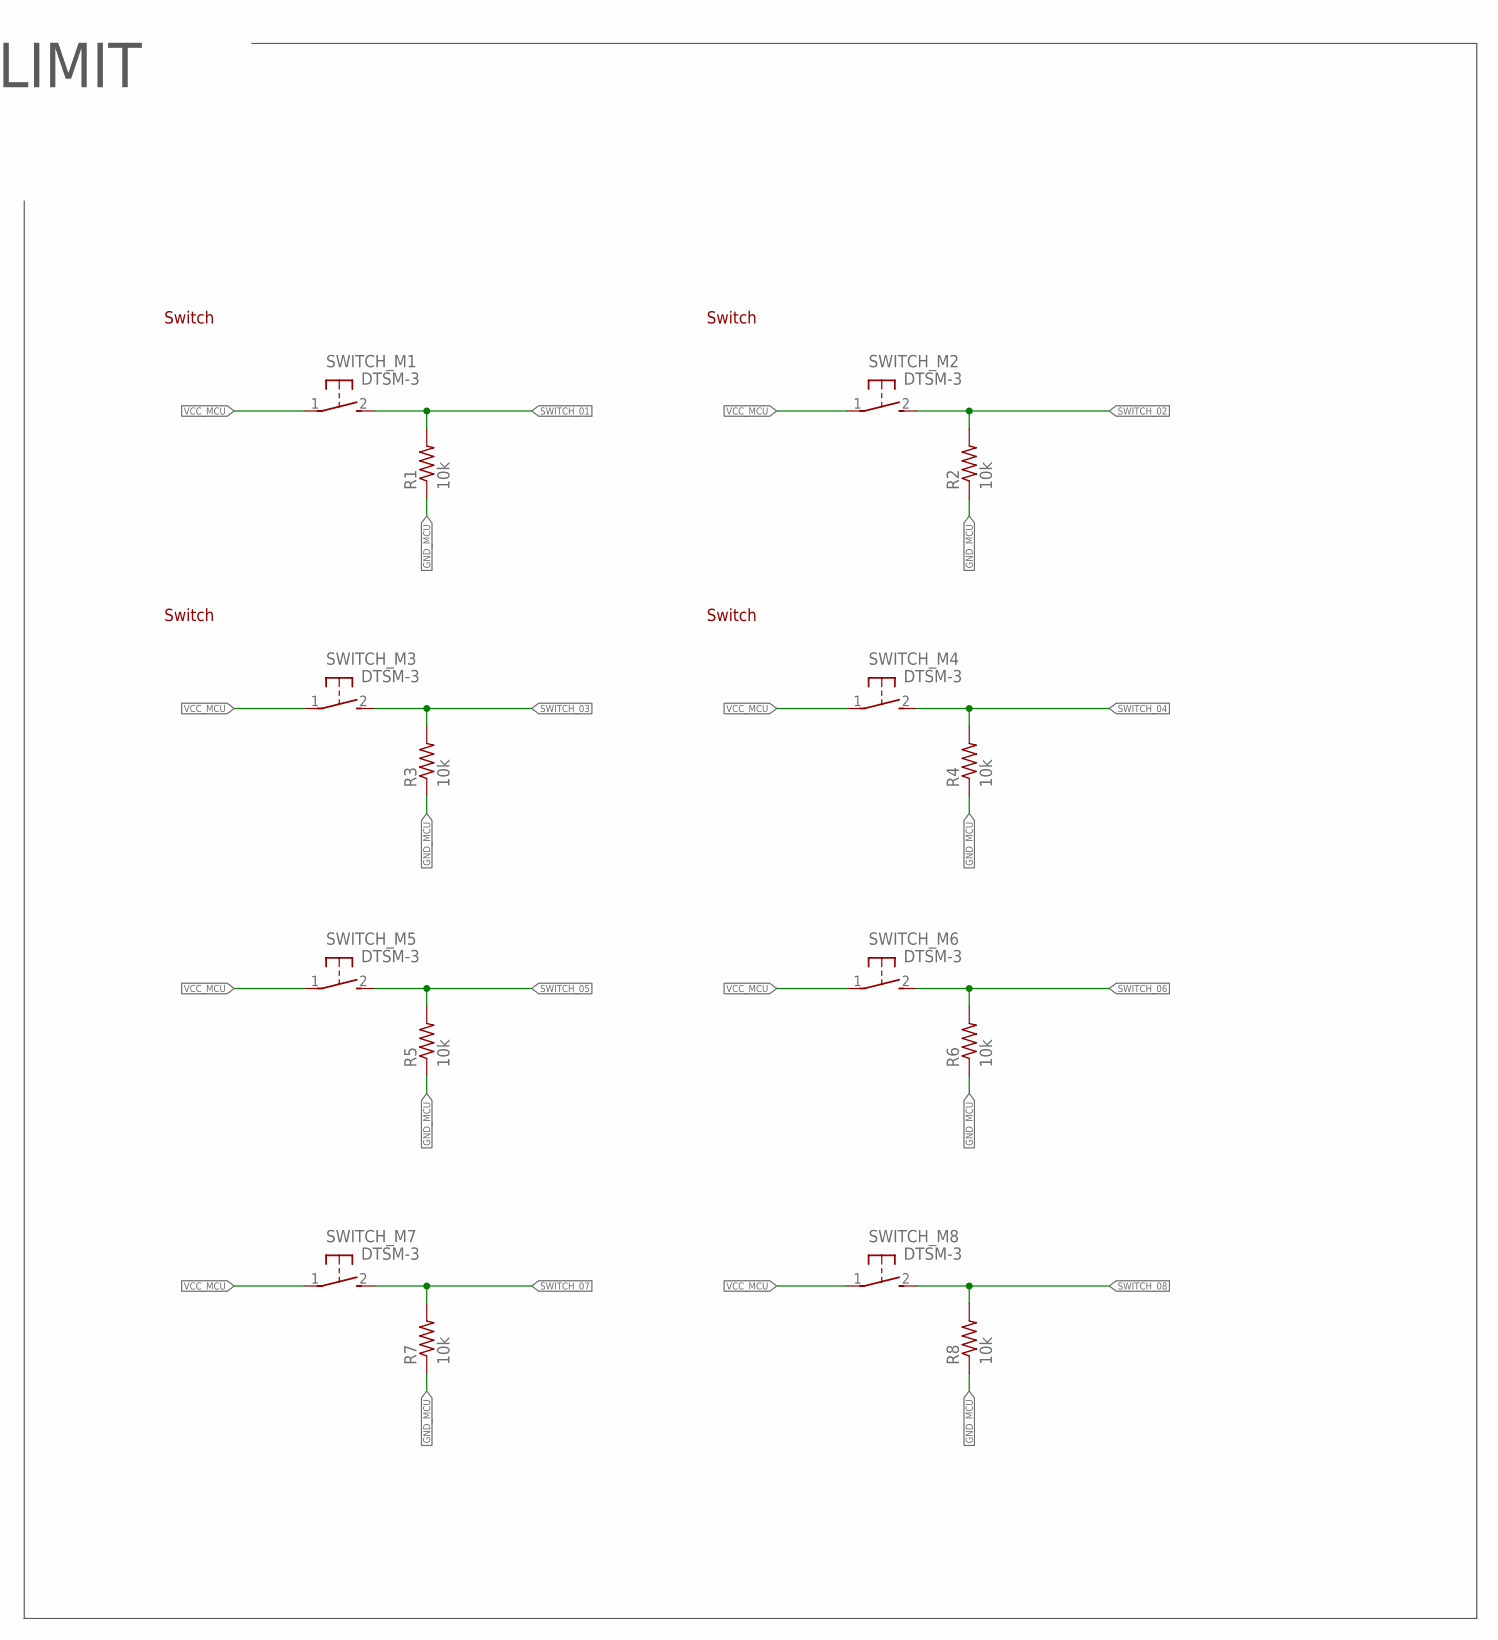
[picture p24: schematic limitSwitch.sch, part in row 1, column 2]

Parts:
J1: CONN_01; 1X01
JP1, JP3: JUMPER-SMT_2_NC_TRACE_NO-SILK; SMT-JUMPER_2_NC_TRACE_NO-SILK
LED_STOP: LEDFAB1206; LED1206FAB
M_01, M_02, M_03: CONN_06SMD-1MM; 1X06-1MM
POWER_LED: LEDFAB1206; LED1206FAB
POWER_LED_RES, POWER_LED_RES1: 500; M0805
R1, R2, R3, R4, R5, R6, R7, R8, R9: 10k; M0805
SWITCH_M1, SWITCH_M2, SWITCH_M3, SWITCH_M4, SWITCH_M5, SWITCH_M6, SWITCH_M7, SWITCH_M8: DTSM-3

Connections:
GND_MCU: LED_STOP.2 (C), M_01.1, M_02.1, M_03.1, POWER_LED.2 (C), R1.1, R2.1, R3.1, R4.1, R5.1, R6.1, R7.1, R8.1, R9.1
LED_IN_1: JP1.1, M_01.4, POWER_LED_RES.2
LED_IN_2: JP3.1, M_01.3, POWER_LED_RES1.2
unnamed: POWER_LED.1 (A), POWER_LED_RES1.1
unnamed: LED_STOP.1 (A), POWER_LED_RES.1
SWITCH_01: JP1.2, M_01.6, M_02.3, R1.2, SWITCH_M1.2
SWITCH_02: JP3.2, M_01.5, M_02.4, R2.2, SWITCH_M2.2
SWITCH_03: M_02.5, R3.2, SWITCH_M3.2
SWITCH_04: M_02.6, R4.2, SWITCH_M4.2
SWITCH_05: M_03.6, R5.2, SWITCH_M5.2
SWITCH_06: M_03.5, R6.2, SWITCH_M6.2
SWITCH_07: M_03.4, R7.2, SWITCH_M7.2
SWITCH_08: M_03.3, R8.2, SWITCH_M8.2
VCC_MCU: J1.1, M_01.2, M_02.2, M_03.2, R9.2, SWITCH_M1.1, SWITCH_M2.1, SWITCH_M3.1, SWITCH_M4.1, SWITCH_M5.1, SWITCH_M6.1, SWITCH_M7.1, SWITCH_M8.1

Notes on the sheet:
CONNECTORS
Connector
LED
Switch
LIMIT

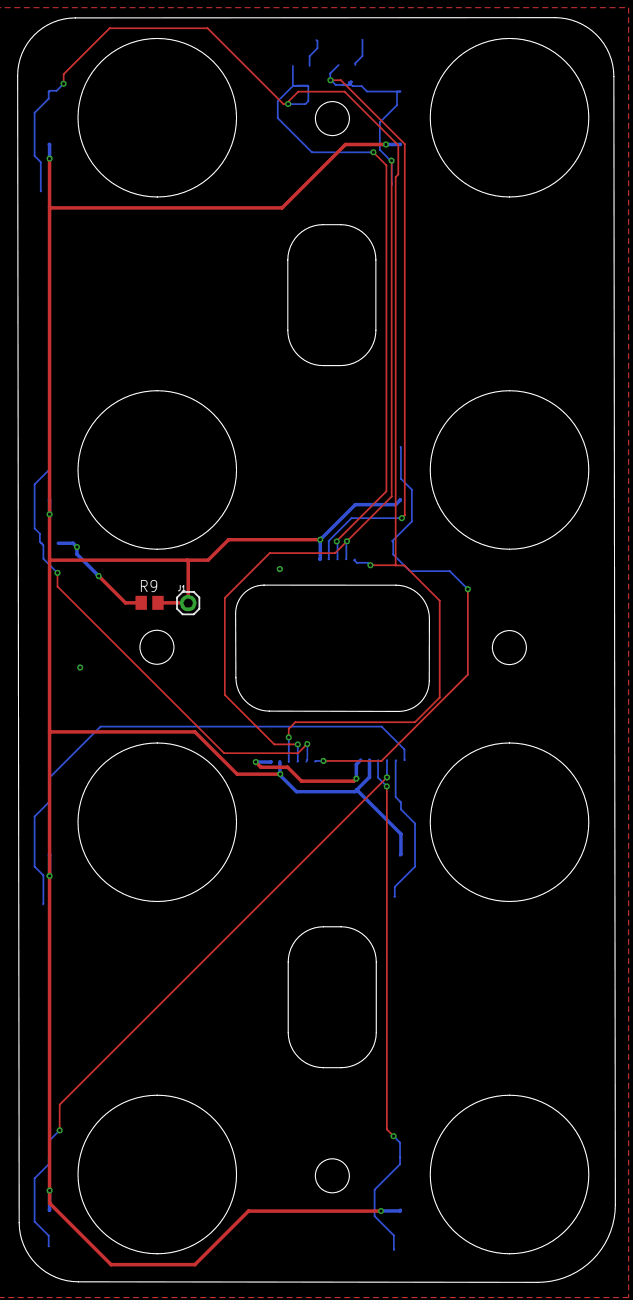
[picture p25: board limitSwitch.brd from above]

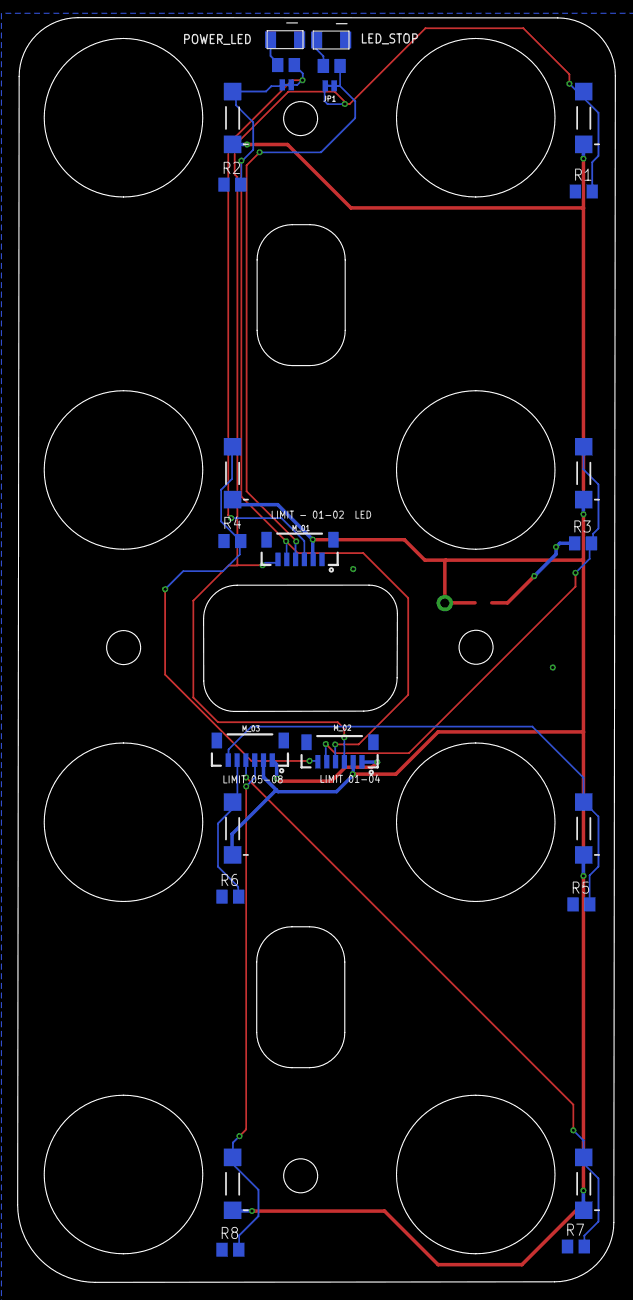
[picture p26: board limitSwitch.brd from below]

Board: 2 copper layers, 67.9 x 143.6 mm, 27 parts (25 on the bottom side), 14 nets.

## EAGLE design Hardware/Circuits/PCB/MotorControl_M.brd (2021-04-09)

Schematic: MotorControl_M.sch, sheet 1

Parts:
C1: 47uf/10V; 0603-CAP
C2, C3, C9: 0.1uF; 0603-CAP
C4, C5, C6, C7, C10: 0.1uf; 0603-CAP
C8: 0.1uF; 0603
C11: 1uf; 0603-CAP
C12: 10uf; C1210
C13, C14, C15, C16, C17, C18, C19: CAPACITOR-1210; C1210
CAN_INPUT, CAN_INPUT1, CAN_INPUT4, CAN_INPUT5: CONN_02-JST-2MM-SMT; JST-2-SMD
CM_01, CM_02, CM_03, CM_04, CM_05, CM_06, CM_07, CM_08: 1X04_STRAIGHT; 1X04-CLEANBIG
D1: S2A; DO214AA
D2, D3, D4, D5, D6, D7, D8, D9: D_SCHOTTKY-SOD123; SOD123
D10: SOD123L; SOD123
J1, J4: CONN_06SMD-1MM; 1X06-1MM
J2, J3: CONN_02; 1X02
J5: CONN_01; 1X01
JP5, JP6: JUMPER-SMT_2_NC_TRACE_NO-SILK; SMT-JUMPER_2_NC_TRACE_NO-SILK
MC1, MC2, MC3, MC4, MC5, MC6, MC7, MC8: 100uF; PANASONIC_D
MCP2562FD, MCP2562_2.0: MCP2562-E/SN; SOIC127P600X175-8N
MOTOR_01, MOTOR_02, MOTOR_03, MOTOR_04, MOTOR_05, MOTOR_06, MOTOR_07, MOTOR_08: DRV8880TMC2209; TMC2209_SMD
P1: M-2X10-87759; 87759-20
PES_D3, PES_D5: PESD1CAN; SOT23
POWER_M: B2P-VH
POWER_MCU: B2P-VH
R1: 0.3; 0805
R2, R3, R5, R6, R9, R11: 10K; 0603-RES
R4, R8: 120; 0603-RES
R7, R12, R13, R16, R17, R18, R19, R20: 100; 0603
R10: 500; 0603-RES
R14: 10k; 0603
R15: 1k; 0603
STATUS_LED: LEDFAB1206; LED1206FAB
SX1509: SX1509; QFN-28
U1: MIC2005; SOT23-6
U2: 74HCT245D,65220-TSSOP; 20-TSSOP
U4: 74HC4051BQ; DHVQFN-16-2.5X3.5MM
U$1: MOSFET_SLIDER
U$3: TEENSY_4.0_WITH_SMD_HEADER_PINS

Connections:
3.3V: C2.1, C3.1, C5.1, C6.1, C9.1, MCP2562FD.5 (VIO), MCP2562_2.0.5 (VIO), P1.19, R2.2, R3.2, R5.2, R6.2, SX1509.4 (VCC1), SX1509.12 (VDDM), SX1509.18 (VCC2), U$3.3.3V, U$3.3.3V1 (3.3V)
!RESET: R3.1, SX1509.23 (!RESET)
CAN_H: CAN_INPUT.1 (2), CAN_INPUT1.1 (2), MCP2562FD.7 (CANH), PES_D3.1, R8.1
CAN_H2: CAN_INPUT4.1 (2), CAN_INPUT5.1 (2), MCP2562_2.0.7 (CANH), PES_D5.1, R4.1
CAN_L: CAN_INPUT.2 (1), CAN_INPUT1.2 (1), J2.2, MCP2562FD.6 (CANL), PES_D3.2
CAN_L2: CAN_INPUT4.2 (1), CAN_INPUT5.2 (1), J3.2, MCP2562_2.0.6 (CANL), PES_D5.2
CAN_RX2: MCP2562_2.0.4 (RXD), U$3.0 (0/RX1/T/CRX2)
CAN_RX3: MCP2562FD.4 (RXD), U$3.30 (30/CRX3)
CAN_TX2: MCP2562_2.0.1 (TXD), U$3.1 (1/TX1/T/CTX2)
CAN_TX3: MCP2562FD.1 (TXD), U$3.31 (31/CTX3)
GND_MCU: C1.2, C2.2, C3.2, C4.2, C5.2, C6.2, C7.2, C8.2, C9.2, C10.2, C11.2, C12.1, C13.1, C14.1, C15.1, C16.1, C17.1, C18.1, C19.1, D1.A, J1.1, J4.1, JP5.2, JP6.1, MC1.-, MC2.-, MC3.-, MC4.-, MC5.-, MC6.-, MC7.-, MC8.-, MCP2562FD.2 (VSS), MCP2562FD.8 (STBY), MCP2562_2.0.2 (VSS), MCP2562_2.0.8 (STBY), MOTOR_01.GND_0, MOTOR_01.GND_1, MOTOR_02.GND_0, MOTOR_02.GND_1, MOTOR_03.GND_0, MOTOR_03.GND_1, MOTOR_04.GND_0, MOTOR_04.GND_1, MOTOR_05.GND_0, MOTOR_05.GND_1, MOTOR_06.GND_0, MOTOR_06.GND_1, MOTOR_07.GND_0, MOTOR_07.GND_1, MOTOR_08.GND_0, MOTOR_08.GND_1, P1.18, P1.20, PES_D3.3, PES_D5.3, POWER_M.2, POWER_MCU.2, R14.2, STATUS_LED.2 (C), SX1509.3 (GND), SX1509.17 (GND), SX1509.29 (GND), U1.2 (GND), U2.10 (GND), U2.19 (~OE), U4.7 (VEE), U4.8 (GND), U$1.GND_1, U$1.GND_2, U$1.GND_3, U$1.GND_4, U$3.GND, U$3.GND1 (GND), U$3.GND2 (GND)
INPUT_01: J5.1, P1.16
INPUT_02: J4.3, P1.14
INT_00: R6.1, SX1509.9 (!INT)
INT_01: P1.6, U$3.32
INT_02: P1.8, U$3.33
MA1_01: CM_01.1, MOTOR_01.A1
MA1_02: CM_02.1, MOTOR_02.A1
MA1_03: CM_03.1, MOTOR_03.A1
MA1_04: CM_04.1, MOTOR_04.A1
MA1_05: CM_05.1, MOTOR_05.A1
MA1_06: CM_06.1, MOTOR_06.A1
MA1_07: CM_07.1, MOTOR_07.A1
MA1_08: CM_08.1, MOTOR_08.A1
MA2_01: CM_01.2, MOTOR_01.A2
MA2_02: CM_02.2, MOTOR_02.A2
MA2_03: CM_03.2, MOTOR_03.A2
MA2_04: CM_04.2, MOTOR_04.A2
MA2_05: CM_05.2, MOTOR_05.A2
MA2_06: CM_06.2, MOTOR_06.A2
MA2_07: CM_07.2, MOTOR_07.A2
MA2_08: CM_08.2, MOTOR_08.A2
MB1_01: CM_01.4, MOTOR_01.B1
MB1_02: CM_02.4, MOTOR_02.B1
MB1_03: CM_03.4, MOTOR_03.B1
MB1_04: CM_04.4, MOTOR_04.B1
MB1_05: CM_05.4, MOTOR_05.B1
MB1_06: CM_06.4, MOTOR_06.B1
MB1_07: CM_07.4, MOTOR_07.B1
MB1_08: CM_08.4, MOTOR_08.B1
MB2_01: CM_01.3, MOTOR_01.B2
MB2_02: CM_02.3, MOTOR_02.B2
MB2_03: CM_03.3, MOTOR_03.B2
MB2_04: CM_04.3, MOTOR_04.B2
MB2_05: CM_05.3, MOTOR_05.B2
MB2_06: CM_06.3, MOTOR_06.B2
MB2_07: CM_07.3, MOTOR_07.B2
MB2_08: CM_08.3, MOTOR_08.B2
MDIR_01: MOTOR_01.DIR, U$3.6
MDIR_02: MOTOR_02.DIR, U$3.8 (8/TX2)
MDIR_03: MOTOR_03.DIR, U$3.10 (10/CS)
MDIR_04: MOTOR_04.DIR, U$3.12 (12/MISO)
MDIR_05: MOTOR_05.DIR, U$3.17/A3 (17/A3/SDA1)
MDIR_06: MOTOR_06.DIR, U$3.3
MDIR_07: MOTOR_07.DIR, U$3.23/A9 (23/A9/CRX1)
MDIR_08: MOTOR_08.DIR, U$3.27 (27/A13/SCK1)
MOTOR_MUX_RX: R15.1, U4.3 (Z), U$3.21/A7 (21/A7/RX5)
MOTOR_MUX_TX: R15.2, U$3.20/A6 (20/A6/TX5)
MOTOR_TX_RX_01: MOTOR_01.TX/RX, U4.13 (Y0)
MOTOR_TX_RX_02: MOTOR_02.TX/RX, U4.14 (Y1)
MOTOR_TX_RX_03: MOTOR_03.TX/RX, U4.15 (Y2)
MOTOR_TX_RX_04: MOTOR_04.TX/RX, U4.12 (Y3)
MOTOR_TX_RX_05: MOTOR_05.TX/RX, U4.1 (Y4)
MOTOR_TX_RX_06: MOTOR_06.TX/RX, U4.5 (Y5)
MOTOR_TX_RX_07: MOTOR_07.TX/RX, U4.2 (Y6)
MOTOR_TX_RX_08: MOTOR_08.TX/RX, U4.4 (Y7)
MSTEP_01: MOTOR_01.STEP, U$3.5
MSTEP_02: MOTOR_02.STEP, U$3.7 (7/RX2)
MSTEP_03: MOTOR_03.STEP, U$3.9
MSTEP_04: MOTOR_04.STEP, U$3.11 (11/MOSI)
MSTEP_05: MOTOR_05.STEP, U$3.16/A2 (16/A2/SCL1)
MSTEP_06: MOTOR_06.STEP, U$3.2
MSTEP_07: MOTOR_07.STEP, U$3.22/A8 (22/A8/CTX1)
MSTEP_08: MOTOR_08.STEP, U$3.26 (26/A12/MOSI1)
unnamed: J2.1, R8.2
unnamed: J3.1, R4.2
unnamed: D10.C, U$3.VIN
unnamed: R7.1, U2.18 (B0)
unnamed: R12.1, U2.17 (B1)
unnamed: R13.1, U2.16 (B2)
unnamed: R11.2, U1.4 (!FAULT)
unnamed: R16.1, U2.15 (B3)
unnamed: R17.1, U2.14 (B4)
unnamed: R9.2, U1.3 (EN)
unnamed: R18.1, U2.13 (B5)
unnamed: R19.1, U2.12 (B6)
unnamed: R20.1, U2.11 (B7)
unnamed: R10.1, STATUS_LED.1 (A)
NEOPIXEL_01_3V: U2.2 (A0), U$3.4
NEOPIXEL_01_5V: P1.1, R7.2
NEOPIXEL_02_3V: U2.3 (A1), U$3.13 (13/SCK/LED)
NEOPIXEL_02_5V: P1.3, R12.2
NEOPIXEL_03_3V: U2.4 (A2), U$3.14/A0 (14/A0/TX3)
NEOPIXEL_03_5V: P1.5, R13.2
NEOPIXEL_04_3V: U2.5 (A3), U$3.15/A1 (15/A1/RX3)
NEOPIXEL_04_5V: P1.7, R16.2
NEOPIXEL_05_3V: U2.6 (A4), U$3.24 (24/A10/SCL2)
NEOPIXEL_05_5V: P1.9, R17.2
NEOPIXEL_06_3V: U2.7 (A5), U$3.25 (25/A11/SDA2)
NEOPIXEL_06_5V: P1.11, R18.2
NEOPIXEL_07_3V: U2.8 (A6), U$3.28 (28/RX7)
NEOPIXEL_07_5V: P1.13, R19.2
NEOPIXEL_08_3V: U2.9 (A7), U$3.29 (29/TX7)
NEOPIXEL_08_5V: P1.15, R20.2
OSCIO: SX1509.11 (OSCIO)
RESET: P1.10, U$3.RESET
STATUS_PIN: P1.12, R10.2
SX00_0: MOTOR_06.ENA (ENABLE), SX1509.27 (I/O[0])
SX00_1: J1.3, SX1509.28 (I/O[1])
SX00_2: MOTOR_04.ENA (ENABLE), SX1509.1 (I/O[2])
SX00_3: J1.4, SX1509.2 (I/O[3])
SX00_4: MOTOR_03.ENA (ENABLE), SX1509.5 (I/O[4])
SX00_5: J4.4, SX1509.6 (I/O[5]), U4.11 (S0)
SX00_6: MOTOR_02.ENA (ENABLE), SX1509.7 (I/O[6])
SX00_7: J4.5, SX1509.8 (I/O[7]), U4.10 (S1)
SX00_8: MOTOR_05.ENA (ENABLE), SX1509.13 (I/O[8])
SX00_9: J4.6, SX1509.14 (I/O[9]), U4.9 (S2)
SX00_10: MOTOR_01.ENA (ENABLE), SX1509.15 (I/O[10])
SX00_11: R14.1, SX1509.16 (I/O[11]), U4.6 (!E!)
SX00_12: MOTOR_07.ENA (ENABLE), SX1509.19 (I/O[12])
SX00_13: J1.5, SX1509.20 (I/O[13])
SX00_14: MOTOR_08.ENA (ENABLE), SX1509.21 (I/O[14])
SX00_15: J1.6, SX1509.22 (I/O[15])
SX00_ADDR0: JP5.1, SX1509.26 (ADDR0)
SX00_ADDR1: JP6.2, SX1509.10 (ADDR1)
SX00_SCL: P1.4, R5.1, SX1509.25 (SCL), U$3.19/A5 (19/A5/SCL0)
SX00_SDA: P1.2, R2.1, SX1509.24 (SDA), U$3.18/A4 (18/A4/SDA0)
VBAT: U$3.VBAT
VCC_5VREG: C4.1, C8.1, C10.1, C11.1, D2.A, D3.A, D4.A, D5.A, D6.A, D7.A, D8.A, D9.A, D10.A, J1.2, J4.2, MCP2562FD.3 (VDD), MCP2562_2.0.3 (VDD), MOTOR_01.5V (FAULT), MOTOR_02.5V (FAULT), MOTOR_03.5V (FAULT), MOTOR_04.5V (FAULT), MOTOR_05.5V (FAULT), MOTOR_06.5V (FAULT), MOTOR_07.5V (FAULT), MOTOR_08.5V (FAULT), U1.6 (VOUT), U2.1 (DIR), U2.20 (VCC), U4.16 (VCC), U4.EP (VCC)
VCC_LEDS: D1.C, P1.17, R1.1
VCC_M: C12.2, C13.2, C14.2, C15.2, C16.2, C17.2, C18.2, C19.2, D2.C, D3.C, D4.C, D5.C, D6.C, D7.C, D8.C, D9.C, MC1.+, MC2.+, MC3.+, MC4.+, MC5.+, MC6.+, MC7.+, MC8.+, MOTOR_01.VM, MOTOR_02.VM, MOTOR_03.VM, MOTOR_04.VM, MOTOR_05.VM, MOTOR_06.VM, MOTOR_07.VM, MOTOR_08.VM, POWER_M.1
VCC_MCU: POWER_MCU.1, U$1.VIN_1, U$1.VIN_2
VCC_SWITCH: C1.1, C7.1, R1.2, R9.1, R11.1, U1.1 (VIN), U$1.VOUT_1, U$1.VOUT_2

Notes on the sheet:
MICROCONTROLLER
INPUTS
MOTOR DRIVERS
CAN BUS
CAN Bus output
Input power line for the BRD
INFO
REGULATOR
IC2 MUX 01
The VCC1/2 jumpers (SJ2, SJ3) set those pins to 3.3V.
I2C Addresses [ADDR1][ADDR0]: 00 - 0x3E (default) 01 - 0x3F 10 - 0x70 11 - 0x71
SJ1 enables/disables 10k pull-up resistors on the SDA and SCL lines. (Default: closed)
SJ4 and SJ5 set the I2c address of the SX1509.
SX1509
I2C Address Select
I2C Pull-up Resistors
VDD Range: 1.425-3.6V
Allowable VCC1/2 Range: 1.2-3.6V
JP1 shorts VEE to GND, if a bi-polar supply is not used. (Defaults closed.)
R1 keeps enable active (low). Pull !E! directly to VCC to disable the mux.

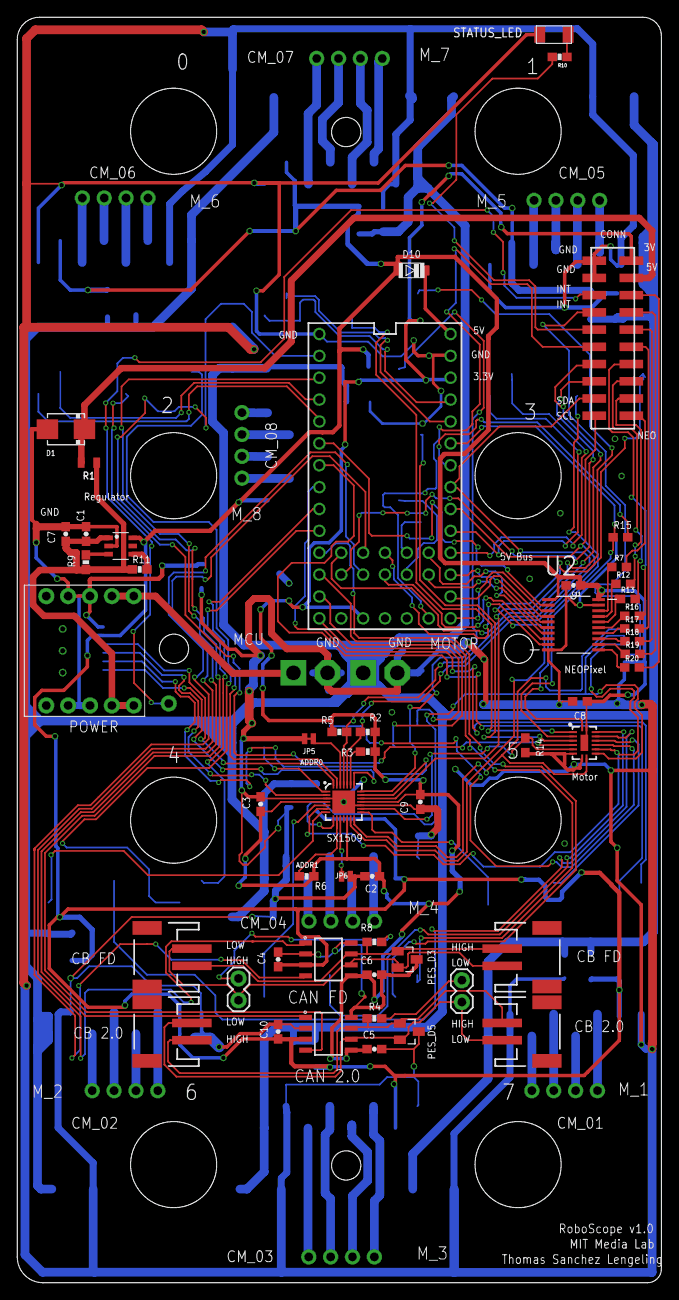
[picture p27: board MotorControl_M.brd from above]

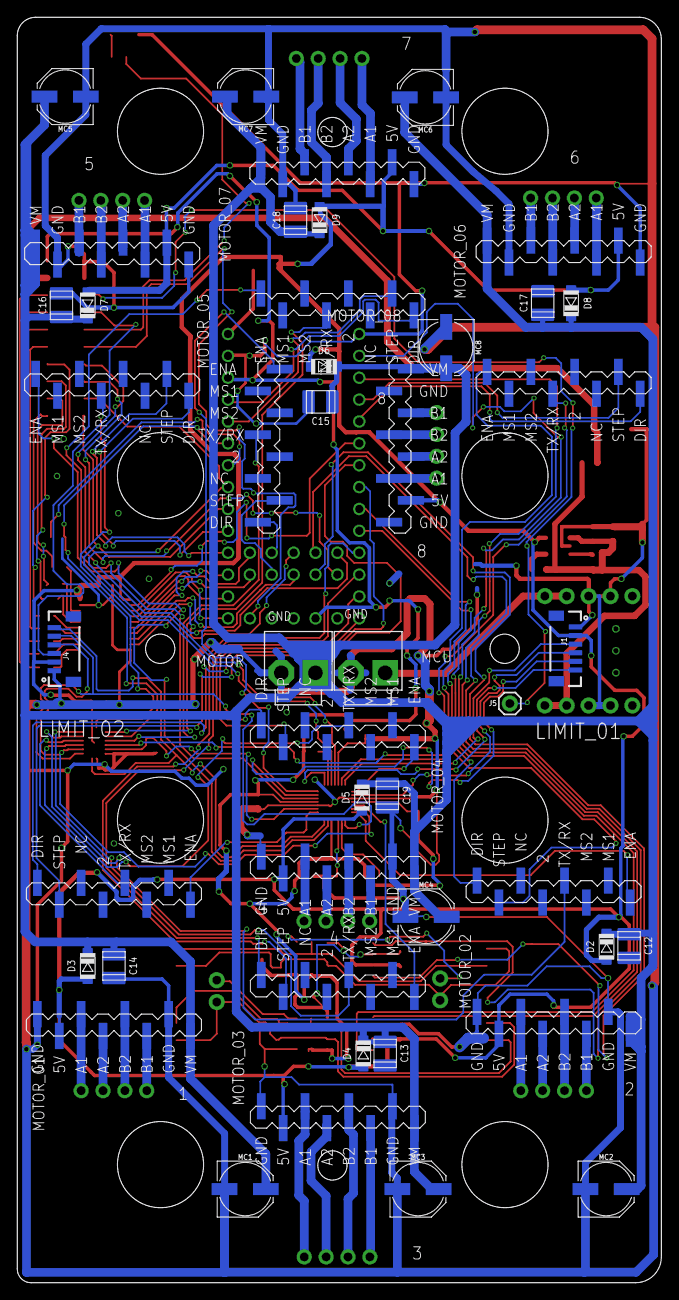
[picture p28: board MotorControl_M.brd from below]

Board: 2 copper layers, 74.8 x 147.0 mm, 99 parts (37 on the bottom side), 131 nets.

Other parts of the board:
DRILEGEND: DRILEGEND

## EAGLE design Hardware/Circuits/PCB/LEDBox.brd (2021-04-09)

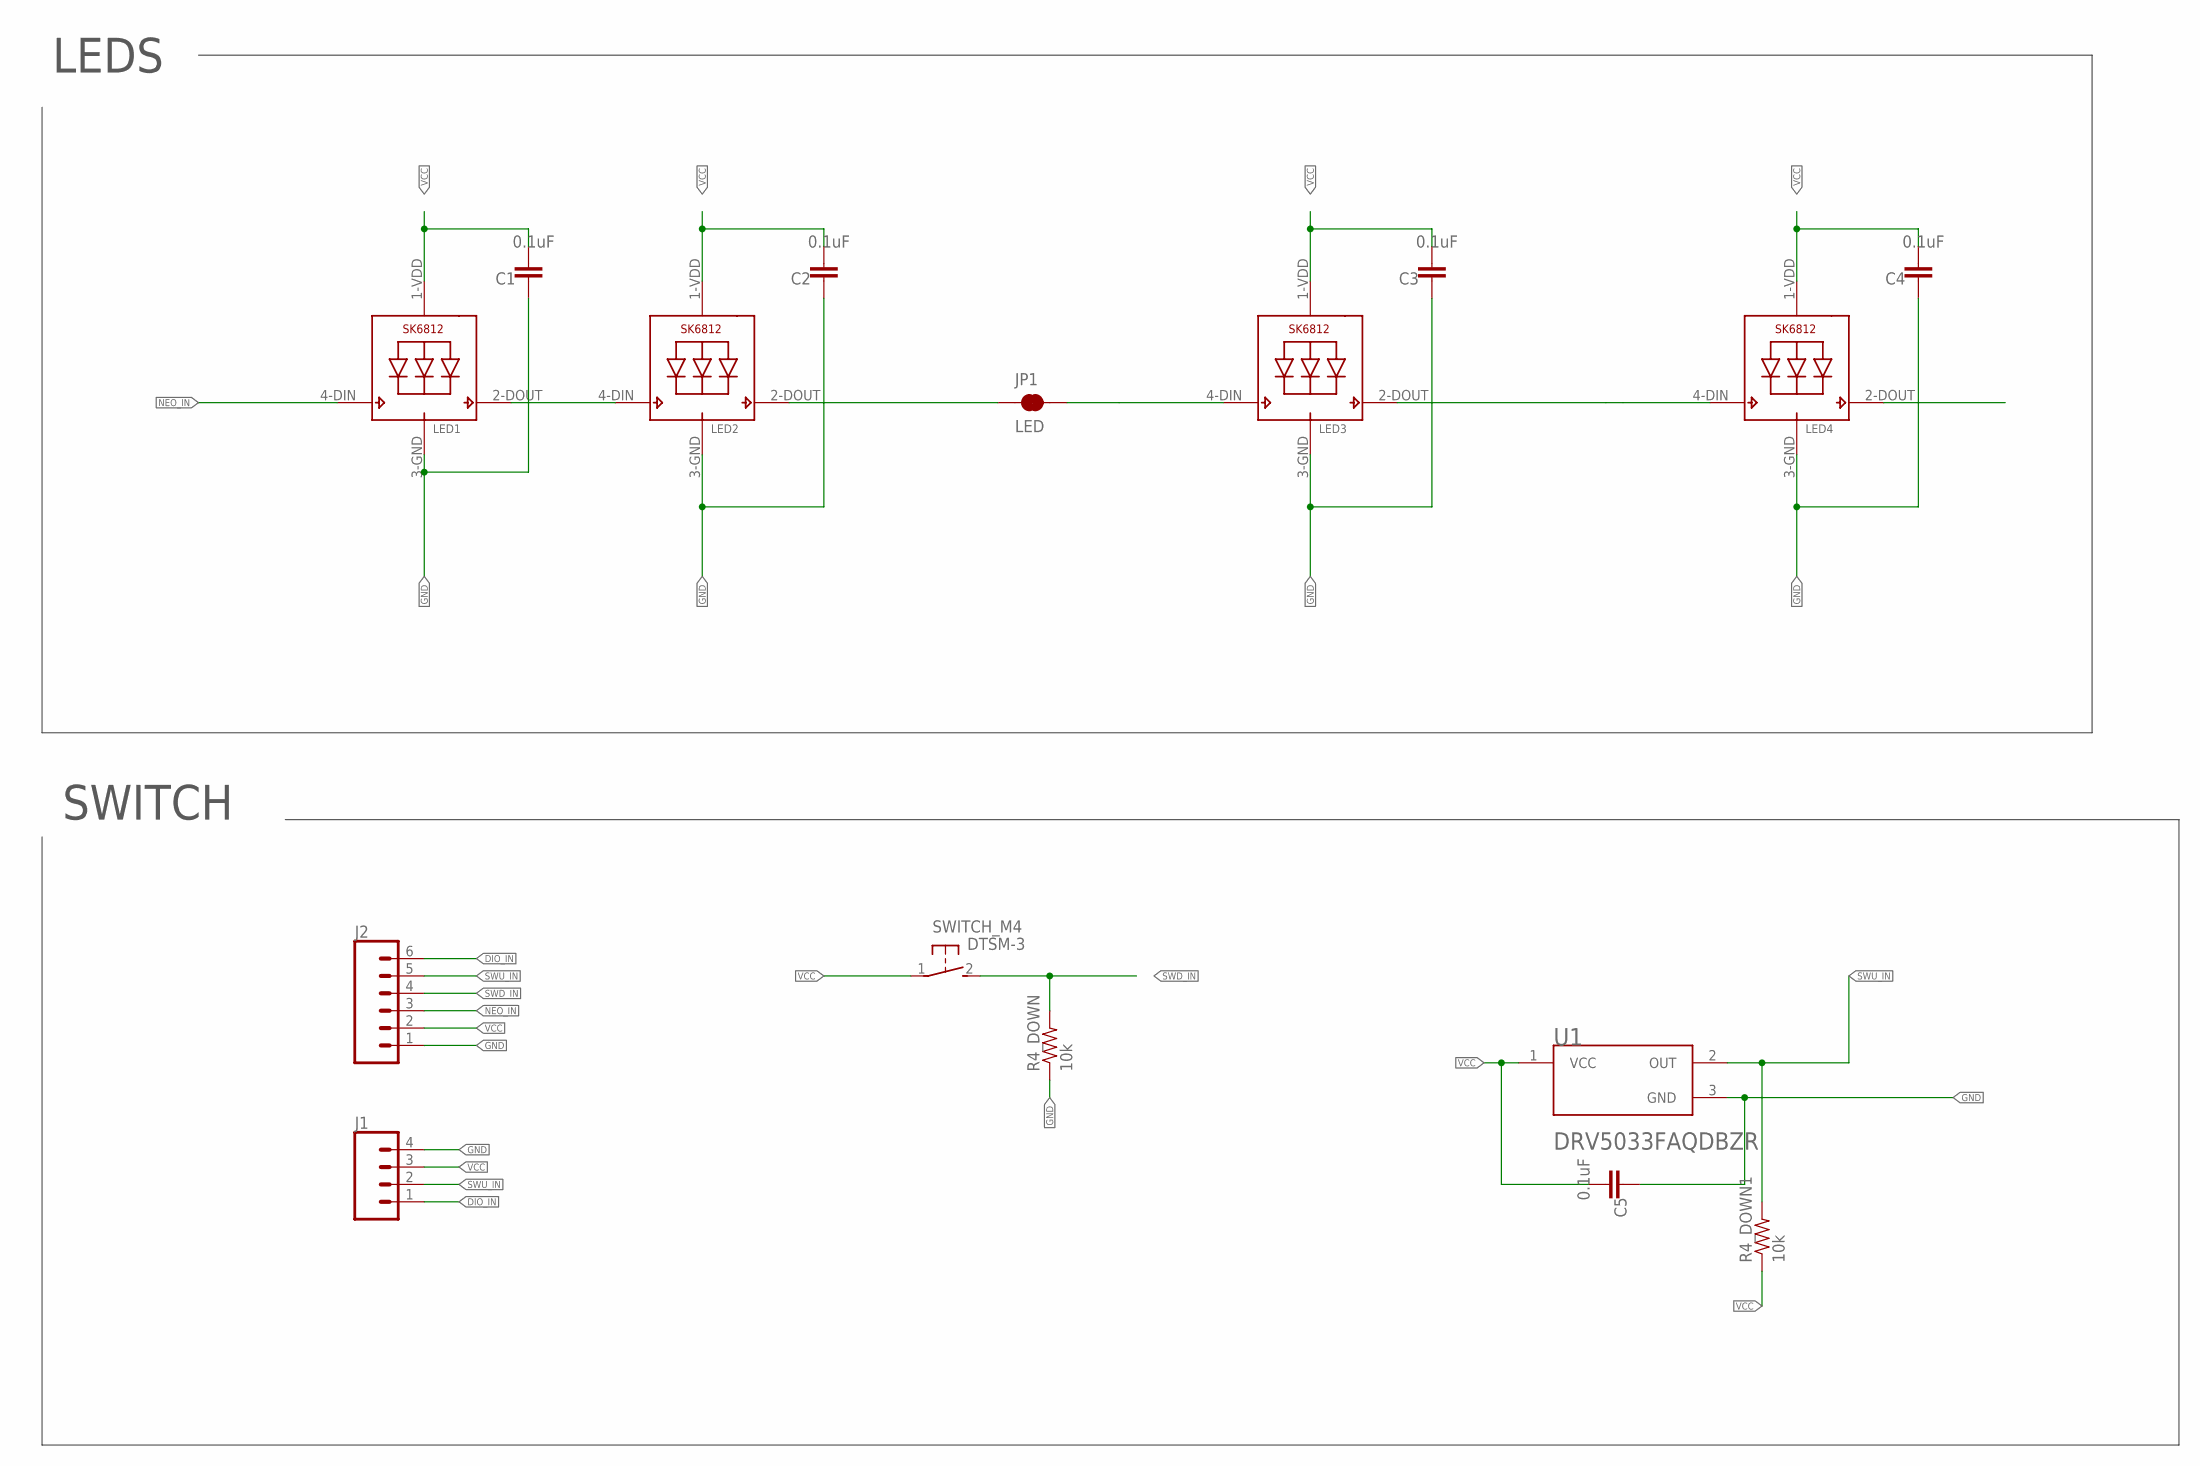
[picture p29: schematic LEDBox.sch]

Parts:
C1, C2, C3, C4, C5: 0.1uF; 0603
J1: CONN_041X04_NO_SILK; 1X04_NO_SILK
J2: CONN_06SMD-1MM; 1X06-1MM
JP1: LED; SMT-JUMPER_2_NC_TRACE_NO-SILK
LED1, LED2, LED3, LED4: SK6812_5050W; LED5050_W
R4_DOWN, R4_DOWN1: 10k; 0603
SWITCH_M4: DTSM-3
U1: TEXAS_INSTRUMENTS_DRV5033FAQDBZRTEXAS_INSTRUMENTS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; TEXAS_INSTRUMENTS_DRV5033FAQDBZR_0

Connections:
DIO_IN: J1.1, J2.6
GND: C1.1, C2.1, C3.1, C4.1, C5.1, J1.4, J2.1, LED1.3-GND (GND), LED2.3-GND (GND), LED3.3-GND (GND), LED4.3-GND (GND), R4_DOWN.1, U1.3 (GND)
unnamed: LED1.2-DOUT (DO), LED2.4-DIN (DI)
unnamed: JP1.1, LED2.2-DOUT (DO)
unnamed: JP1.2, LED3.4-DIN (DI)
unnamed: LED3.2-DOUT (DO), LED4.4-DIN (DI)
NEO_IN: J2.3, LED1.4-DIN (DI)
SWD_IN: J2.4, R4_DOWN.2, SWITCH_M4.2
SWU_IN: J1.2, J2.5, R4_DOWN1.2, U1.2 (OUT)
VCC: C1.2, C2.2, C3.2, C4.2, C5.2, J1.3, J2.2, LED1.1-VDD (VDD), LED2.1-VDD (VDD), LED3.1-VDD (VDD), LED4.1-VDD (VDD), R4_DOWN1.1, SWITCH_M4.1, U1.1 (VCC)

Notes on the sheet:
LEDS
SWITCH


Board: 2 copper layers, 29.5 x 29.5 mm, 16 parts (1 on the bottom side), 10 nets.

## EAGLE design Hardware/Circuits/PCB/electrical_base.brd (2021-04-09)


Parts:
D1: WHITE 12V; LED-1206
D2: WHITE 5V; LED-1206
Q1, Q2, Q3, Q4: XT60_YELLOW; AMASS_XT60PB-M
R1, R2: 330; 0603
U$1, U$2: SWITCH_3P_4.7; 3P
X1, X2, X3, X4: B2P-VH

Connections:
5V: Q2.1, Q4.1, U$2.P$1 (1)
5V_S: R2.1, U$2.P$2 (2), X3.1, X4.1
12V: Q1.1, Q3.1, U$1.P$1 (1)
12V_S: R1.1, U$1.P$2 (2), X1.1, X2.1
GND: D1.C, D2.C, Q1.2, Q2.2, Q3.2, Q4.2, X1.2, X2.2, X3.2, X4.2
unnamed: D1.A, R1.2
unnamed: D2.A, R2.2


Board: 2 copper layers, 56.0 x 164.0 mm, 14 parts (0 on the bottom side), 7 nets.

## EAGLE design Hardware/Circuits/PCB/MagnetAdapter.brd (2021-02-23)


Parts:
C1: 0.1uf; C0805
J1: CONN_041X04_NO_SILK; 1X04_NO_SILK
R4_DOWN: 10K; M0805
U1: TEXAS_INSTRUMENTS_DRV5033FAQDBZRTEXAS_INSTRUMENTS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; TEXAS_INSTRUMENTS_DRV5033FAQDBZR_0

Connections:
DIO: J1.2, R4_DOWN.2, U1.2 (OUT)
GND: C1.1, J1.4, U1.3 (GND)
VCC: C1.2, J1.3, R4_DOWN.1, U1.1 (VCC)


Board: 2 copper layers, 9.7 x 10.8 mm, 4 parts (0 on the bottom side), 3 nets.

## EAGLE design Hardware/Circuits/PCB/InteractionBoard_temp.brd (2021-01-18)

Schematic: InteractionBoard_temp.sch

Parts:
C1, C2, C3, C4, C5, C6, C7, C8, C9: 0.1uF; 0603-CAP
J3: F-2X10-DIL-2MM; DIL-2MM-2X10
JP1: JUMPER-SMT_3_1-NC_TRACE_NO-SILK; SMT-JUMPER_3_1-NC_TRACE_NO-SILK
JP6, JP7, JP8, JP9, JP10, JP11: JUMPER-SMT_2_NC_TRACE_NO-SILK; SMT-JUMPER_2_NC_TRACE_NO-SILK
M_01, M_02, M_03, M_04, M_05, M_06, M_07, M_08: CONN_06SMD-1MM; 1X06-1MM
POWE_3.3: LEDFAB1206; LED1206FAB
R1, R2, R3, R5, R6, R7, R8: 10k; M0805
R4: 10K; M0805
R9, R10, R11, R12, R13, R14, R16, R17, R18, R19, R20, R21, R23, R24, R25, R26: 10K; 0603-RES
R27, R28: 500; 0603-RES
RN1, RN2, RN3: 4R-NEXB38V; EXB38V
S1: JS207011SCQNR; SW_JS207011SCQNR
S2: MOMENTARY-SWITCH-SPST-2-SMD-5.2MM; TACTILE_SWITCH_SMD_5.2MM
STATUS_LED: LEDFAB1206; LED1206FAB
SW1: 219-10; CTS-219-10
SWB_1, SWB_2, SWB_3, SWB_4, SWB_5, SWB_6, SWB_7, SWB_8: B3F-1000
SWITCH_M1, SWITCH_M2, SWITCH_M3, SWITCH_M4, SWITCH_M5, SWITCH_M6, SWITCH_M7, SWITCH_M8: DTSM-3
SWR_1, SWR_2, SWR_3, SWR_4, SWR_5, SWR_6, SWR_7, SWR_8: 10K; M0805
U1, U2, U4: SX1509; QFN-28

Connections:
0_SX1: M_04.6, U1.27 (I/O[0])
0_SX2: M_08.6, U2.27 (I/O[0])
0_SX3: U4.27 (I/O[0])
1_SX1: M_04.5, U1.28 (I/O[1])
1_SX2: M_08.5, U2.28 (I/O[1])
1_SX3: J3.16, U4.28 (I/O[1])
2_SX1: M_02.6, U1.1 (I/O[2])
2_SX2: M_06.6, U2.1 (I/O[2])
2_SX3: J3.14, U4.1 (I/O[2])
3.3V: C1.1, C2.1, C3.1, C4.1, C5.1, C6.1, C7.1, C8.1, C9.1, J3.19, R9.2, R10.2, R11.2, R12.2, R13.2, R14.2, R16.2, R17.2, R18.2, R19.2, R20.2, R21.2, R23.2, R24.2, R25.2, R26.2, R27.2, RN1.5 (2), RN1.6 (2), RN1.7 (2), RN1.8 (2), RN2.7 (2), RN2.8 (2), RN3.5 (2), RN3.6 (2), RN3.7 (2), RN3.8 (2), S2.1, S2.2, SWB_1.1, SWB_2.1, SWB_3.1, SWB_4.1, SWB_5.1, SWB_6.1, SWB_7.1, SWB_8.1, SWITCH_M1.1, SWITCH_M2.1, SWITCH_M3.1, SWITCH_M4.1, SWITCH_M5.1, SWITCH_M6.1, SWITCH_M7.1, SWITCH_M8.1, U1.4 (VCC1), U1.12 (VDDM), U1.18 (VCC2), U2.4 (VCC1), U2.12 (VDDM), U2.18 (VCC2), U4.4 (VCC1), U4.12 (VDDM), U4.18 (VCC2)
3_SX1: M_02.5, U1.2 (I/O[3])
3_SX2: M_06.5, U2.2 (I/O[3])
3_SX3: J3.12, U4.2 (I/O[3])
4_SX1: M_02.4, U1.5 (I/O[4])
4_SX2: M_06.4, U2.5 (I/O[4])
4_SX3: JP1.1, U4.5 (I/O[4])
5_SX1: M_04.4, U1.6 (I/O[5])
5_SX2: M_08.4, U2.6 (I/O[5])
5_SX3: R28.2, U4.6 (I/O[5])
6_SX1: R2.2, SWB_2.3, SWITCH_M2.2, SWR_2.2, U1.7 (I/O[6])
6_SX2: R6.2, SWB_6.3, SWITCH_M6.2, SWR_6.2, U2.7 (I/O[6])
6_SX3: RN1.1, SW1.20, U4.7 (I/O[6])
7_SX1: R4.2, SWB_4.3, SWITCH_M4.2, SWR_4.2, U1.8 (I/O[7])
7_SX2: R8.2, SWB_8.3, SWITCH_M8.2, SWR_8.2, U2.8 (I/O[7])
7_SX3: RN1.2 (1), SW1.19, U4.8 (I/O[7])
8_SX1: R1.2, SWB_1.3, SWITCH_M1.2, SWR_1.2, U1.13 (I/O[8])
8_SX2: R5.2, SWB_5.3, SWITCH_M5.2, SWR_5.2, U2.13 (I/O[8])
8_SX3: RN1.3 (1), SW1.18, U4.13 (I/O[8])
9_SX1: R3.2, SWB_3.3, SWITCH_M3.2, SWR_3.2, U1.14 (I/O[9])
9_SX2: R7.2, SWB_7.3, SWITCH_M7.2, SWR_7.2, U2.14 (I/O[9])
9_SX3: RN1.4 (1), SW1.17, U4.14 (I/O[9])
10_SX1: M_01.6, U1.15 (I/O[10])
10_SX2: M_05.6, U2.15 (I/O[10])
10_SX3: RN3.1, SW1.16, U4.15 (I/O[10])
11_SX1: M_01.5, U1.16 (I/O[11])
11_SX2: M_05.5, U2.16 (I/O[11])
11_SX3: RN3.2 (1), SW1.15, U4.16 (I/O[11])
12_SX1: M_01.4, U1.19 (I/O[12])
12_SX2: M_05.4, U2.19 (I/O[12])
12_SX3: RN3.3 (1), SW1.14, U4.19 (I/O[12])
13_SX1: M_03.6, U1.20 (I/O[13])
13_SX2: M_07.6, U2.20 (I/O[13])
13_SX3: RN3.4 (1), SW1.13, U4.20 (I/O[13])
14_SX1: M_03.5, U1.21 (I/O[14])
14_SX2: M_07.5, U2.21 (I/O[14])
14_SX3: RN2.1, SW1.12, U4.21 (I/O[14])
15_SX1: M_03.4, U1.22 (I/O[15])
15_SX2: M_07.4, U2.22 (I/O[15])
15_SX3: RN2.2 (1), SW1.11, U4.22 (I/O[15])
!INT_SX3: R24.1, U4.9 (!INT)
!RESET_SX1: R9.1, U1.23 (!RESET)
!RESET_SX2: R16.1, U2.23 (!RESET)
!RESET_SX3: R14.1, U4.23 (!RESET)
ADDR0_SX1: JP8.1, U1.26 (ADDR0)
ADDR0_SX2: JP7.1, U2.26 (ADDR0)
ADDR0_SX3: JP11.1, U4.26 (ADDR0)
ADDR1_SX1: JP9.1, U1.10 (ADDR1)
ADDR1_SX2: JP6.1, U2.10 (ADDR1)
ADDR1_SX3: JP10.1, U4.10 (ADDR1)
GND_MCU: C1.2, C2.2, C3.2, C4.2, C5.2, C6.2, C7.2, C8.2, C9.2, J3.18, J3.20, JP7.2, JP9.2, M_01.1, M_02.1, M_03.1, M_04.1, M_05.1, M_06.1, M_07.1, M_08.1, POWE_3.3.2 (C), R1.1, R2.1, R3.1, R4.1, R5.1, R6.1, R7.1, R8.1, RN2.3 (1), STATUS_LED.2 (C), SW1.1, SW1.2, SW1.3, SW1.4, SW1.5, SW1.6, SW1.7, SW1.8, SW1.9, SW1.10, SWR_1.1, SWR_2.1, SWR_3.1, SWR_4.1, SWR_5.1, SWR_6.1, SWR_7.1, SWR_8.1, U1.3 (GND), U1.17 (GND), U1.29 (GND), U2.3 (GND), U2.17 (GND), U2.29 (GND), U4.3 (GND), U4.17 (GND), U4.29 (GND)
INT_01: J3.6, R12.1, U1.9 (!INT)
INT_02: J3.8, R19.1, U2.9 (!INT)
unnamed: JP6.2, R21.1
unnamed: JP8.2, R13.1
unnamed: R28.1, STATUS_LED.1 (A)
unnamed: JP10.2, R25.1
unnamed: JP11.2, R26.1
unnamed: POWE_3.3.1 (A), R27.1
NEOPIXEL_01: J3.1, M_01.3
NEOPIXEL_02: J3.3, M_02.3
NEOPIXEL_03: J3.5, M_03.3
NEOPIXEL_04: J3.7, M_04.3
NEOPIXEL_05: J3.9, M_05.3
NEOPIXEL_06: J3.11, M_06.3
NEOPIXEL_07: J3.13, M_07.3
NEOPIXEL_08: J3.15, M_08.3
OSCIO_SX1: U1.11 (OSCIO)
OSCIO_SX2: U2.11 (OSCIO)
OSCIO_SX3: U4.11 (OSCIO)
RESET: J3.10, JP1.2, JP1.3, RN2.6 (2), S2.3, S2.4
SCL_00: J3.4, R11.1, R18.1, R23.1, U1.25 (SCL), U2.25 (SCL), U4.25 (SCL)
SDA_00: J3.2, R10.1, R17.1, R20.1, U1.24 (SDA), U2.24 (SDA), U4.24 (SDA)
VCC_5V: M_01.2, M_02.2, M_03.2, M_04.2, M_05.2, M_06.2, M_07.2, M_08.2, S1.4, S1.8
VCC_5V_IN: J3.17, S1.3, S1.7

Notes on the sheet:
INPUTS
Input power line for the BRD
I2C MUX
SWITCH
CONNECTORS
INFO
The VCC1/2 jumpers (SJ2, SJ3) set those pins to 3.3V.
I2C Address Select
VDD Range: 1.425-3.6V
Allowable VCC1/2 Range: 1.2-3.6V
IC2 MUX 01
IC2 MUX 02
IC2 MUX 03


Board: 2 copper layers, 72.1 x 146.3 mm, 86 parts (0 on the bottom side), 80 nets.

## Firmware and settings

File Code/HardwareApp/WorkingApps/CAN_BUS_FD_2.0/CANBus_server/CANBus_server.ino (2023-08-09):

#include <FlexCAN_T4.h>
#include <string.h>
#include "message.h"
#include <Bounce2.h>
#include <Keyboard.h>

#define NUM_PIXELS 8
#define MSG_SIZE 64
#define NUM_PANELS 12
#define  STATUS_PIN_SX03 5 

FlexCAN_T4FD<CAN3, RX_SIZE_256, TX_SIZE_32> canBusFD;

//key pins
const int KEY_PIN_01 = 6;
const int KEY_PIN_02 = 7;
const int KEY_PIN_03 = 8;
const int KEY_PIN_04 = 9;

const int LED_15 = 22;
const int LED_16 = 23;

Bounce2::Button buttonKey_01 = Bounce2::Button();
Bounce2::Button buttonKey_02 = Bounce2::Button();
Bounce2::Button buttonKey_03 = Bounce2::Button();
Bounce2::Button buttonKey_04 = Bounce2::Button();

byte tempBuffer[768];  // temp buffer
byte fullBoard[768];   // real buffer
int nodeId = 0;
int pixelId = 0;
int numsTimes = 0;

struct Pixel {
  byte b1;
  byte b2;
  byte motorByte;
  byte modeByte;
  byte density;
  byte colorR;
  byte colorG;
  byte colorB;
};

void setup() {
  Serial.begin(115200);
  establishContact();  // Send byte to establish contact until receiver responds
  pinMode(LED_15, OUTPUT);


  canBusFD.begin();
  CANFD_timings_t config;
  config.clock = CLK_40MHz;  //40 CLK_80MHz
  config.baudrate = 1000000;
  config.baudrateFD = 8000000;
  config.propdelay = 190;
  config.bus_length = 1;
  config.sample = 87.5;
  canBusFD.setRegions(64);
  canBusFD.setBaudRate(config);
  canBusFD.mailboxStatus();

  buttonKey_01.attach(KEY_PIN_01, INPUT_PULLUP);
  buttonKey_02.attach(KEY_PIN_02, INPUT_PULLUP);
  buttonKey_03.attach(KEY_PIN_03, INPUT_PULLUP);
  buttonKey_04.attach(KEY_PIN_04, INPUT_PULLUP);

  // DEBOUNCE INTERVAL IN MILLISECONDS
  buttonKey_01.interval(20);
  buttonKey_02.interval(20);
  buttonKey_03.interval(20);
  buttonKey_04.interval(20);

  // INDICATE THAT THE LOW STATE CORRESPONDS TO PHYSICALLY PRESSING THE BUTTON
  buttonKey_01.setPressedState(LOW);
  buttonKey_02.setPressedState(LOW);
  buttonKey_03.setPressedState(LOW);
  buttonKey_04.setPressedState(LOW);

  Serial.println("Server initialization complete.");
}


void loop() {
  //key
  buttonKey_01.update();
  buttonKey_02.update();
  buttonKey_03.update();
  buttonKey_04.update();

  //key
  int keyPin01 = buttonKey_01.pressed();
  int keyPin02 = buttonKey_02.pressed();
  int keyPin03 = buttonKey_03.pressed();
  int keyPin04 = buttonKey_04.pressed();

  if (Serial.available() > 1) {                   // # of bytes available in the serial port
    int len = Serial.readBytes(tempBuffer, 768);  // if there are bytes avilable to read, read them and store in tempBuffer.
    for (int i = 0; i < 768; i++) {
      if (tempBuffer[i] != fullBoard[i]) {
        memcpy(fullBoard, tempBuffer, 768);
        break;
      }
    }
    
    for (int j = 0; j < 12; j++) {
      sendNode(j, fullBoard);
      Serial.println("Node sent");
    }
    numsTimes++;
  }
  else {
    reset(nodeId, pixelId);
  }
}


//resets node and pixel values after going through one iteration of reading.
void reset(int nodeId, int pixelId) {
  nodeId = 0;
  pixelId = 0;
}

void establishContact() {
  while (Serial.available() <= 0) {
    //Serial.write("Good"); // Prints Good to the serial port.
    delay(1000);
  }
}

// Prints current buffer (one node) to serial.
void CANPrint(const CANFD_message_t &msg) {
  Serial.print("Buffer: "); 
  for (uint8_t i = 0; i < msg.len; i++) {
    Serial.print(msg.buf[i], DEC); Serial.print(" ") ;
  }
  Serial.println();
}

void sendNode(int nodeId, byte* buffer) {
  CANMotorMessage msg = CANMotorMessage(nodeId);
  for (int i = 0; i < NUM_PIXELS; i++) {
    msg.addMessage(i, 0, 0, fullBoard[2 + 64 * nodeId + 8 * i], fullBoard[3 + 64 * nodeId + 8 * i], fullBoard[4 + 64 * nodeId + 8 * i], fullBoard[5 + 64 * nodeId + 8 * i], fullBoard[6 + 64 * nodeId + 8 * i], fullBoard[7 + 64 * nodeId + 8 * i]);
  }

  canBusFD.write(msg.getCANmessage(MSG_SIZE));
  delay(1);
  canBusFD.write(msg.getCANmessage(MSG_SIZE));

}

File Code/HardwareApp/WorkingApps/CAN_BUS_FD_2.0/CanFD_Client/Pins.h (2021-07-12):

/*
 * MOTOR PINS
 *
 * PREFIX G -> Global
*/

//define address
#define  SX1509_ADDRESS_00         0x3E
#define  SX1509_ADDRESS_01         0x3F // 0x3F
#define  SX1509_ADDRESS_10         0x70   ///0x71
#define  SX1509_ADDRESS_11         0x71

/*
 * #define  SX1509_ADDRESS_00         0x3E
#define  SX1509_ADDRESS_01         0x3F // 0x3F
#define  SX1509_ADDRESS_10         0x70   ///0x71
#define  SX1509_ADDRESS_11         0x71

 */

//MOTOR DEFINES
#define SERIAL_PORT Serial5
#define DRIVER_ADDRESS 0b00

#define R_SENSE 0.11f


#define LED_STATUS 19

#define INTERRUPT_PIN_SWITCH_01   32
#define INTERRUPT_PIN_SWITCH_02   33

//MOTOR VALUES
#define GMOTOR_STEPS      200 *321 //200
#define GRPM              120 //120
#define MOTOR_STEPS       256
#define RMS_CURRENT       400



//MOTOR PINS
//MOTOR 1
#define ENABLE_01_SX00     10 // SX Enable
#define DIR_PIN_01          6 // Direction
#define STEP_PIN_01         5 // Step

#define ENABLE_02_SX00      6 //  SX Enable
#define DIR_PIN_02          8 // Direction
#define STEP_PIN_02         7 // Step 

#define ENABLE_03_SX00      4 //  SX Enable
#define DIR_PIN_03          10 // Direction 
#define STEP_PIN_03         9 // Step 

#define ENABLE_04_SX00      2 // SX Enable
#define DIR_PIN_04          12 // Direction
#define STEP_PIN_04         11 // Step

#define ENABLE_05_SX00      8 // SX Enable
#define DIR_PIN_05          17 // Direction
#define STEP_PIN_05         16 // Step 

#define ENABLE_06_SX00      0 // SX Enable
#define DIR_PIN_06          3 // Direction 
#define STEP_PIN_06         2 // Step 

#define ENABLE_07_SX00      12 // SX Enable
#define DIR_PIN_07          23 // Direction 
#define STEP_PIN_07         22 // Step 

#define ENABLE_08_SX00      14 // SX Enable
#define DIR_PIN_08          27 // Direction 
#define STEP_PIN_08         26 // Step 


//NEO PIXELS
#define  NEO_PIN_01        4
#define  NEO_PIN_02       13
#define  NEO_PIN_03       14//2;
#define  NEO_PIN_04       15///3;
#define  NEO_PIN_05       24
#define  NEO_PIN_06       25
#define  NEO_PIN_07       28
#define  NEO_PIN_08       29

//LIMIT BUTTONS
#define SWITCH_01_SX01    8 
#define SWITCH_02_SX01    6 
#define SWITCH_03_SX01    9 
#define SWITCH_04_SX01    7 

#define SWITCH_05_SX02    8 
#define SWITCH_06_SX02    6 
#define SWITCH_07_SX02    9 
#define SWITCH_08_SX02    7 

//DOWN BUTTONS
#define DOWN_01_SX01      12 
#define DOWN_02_SX01      4 
#define DOWN_03_SX01      15 
#define DOWN_04_SX01      5 

#define DOWN_05_SX02      12 
#define DOWN_06_SX02      4 
#define DOWN_07_SX02      15 
#define DOWN_08_SX02      5 


//UP BUTTONS
#define  UP_01_SX01       11 
#define  UP_02_SX01       3 
#define  UP_03_SX01       14 
#define  UP_04_SX01       1 

#define  UP_05_SX02       11 
#define  UP_06_SX02       3
#define  UP_07_SX02       14 
#define  UP_08_SX02       1 

//TOUCH PIN
#define  TOUCH_01_SX01    10 
#define  TOUCH_02_SX01    2 
#define  TOUCH_03_SX01    13 
#define  TOUCH_04_SX01    0 

#define  TOUCH_05_SX02    10 
#define  TOUCH_06_SX02    2 
#define  TOUCH_07_SX02    13
#define  TOUCH_08_SX02    0 


//DIP SWITCH
#define  DIP_01_SX03      6 
#define  DIP_02_SX03      7 
#define  DIP_03_SX03      8 
#define  DIP_04_SX03      9 
#define  DIP_05_SX03      10
#define  DIP_06_SX03      11 
#define  DIP_07_SX03      12 
#define  DIP_08_SX03      13 
#define  DIP_09_SX03      14 
#define  DIP_10_SX03      15

//STATUS PIN
#define  STATUS_PIN_SX03  5 

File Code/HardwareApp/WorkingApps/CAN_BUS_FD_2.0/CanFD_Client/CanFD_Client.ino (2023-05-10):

/*
   Can Bus Client
   Sending Can Bus FD
   Sending Can TD 0
*/
#include <FlexCAN_T4.h>
#include "message.h"
#include <SparkFunSX1509.h>
#include "Pins.h"
#include <Wire.h>

#define MSG_SIZE           32

//dip switch  and status
SX1509 sx03;

//CAN BUS FD
FlexCAN_T4FD<CAN3, RX_SIZE_256, TX_SIZE_32>   FD;   // fd port

//CAN BUS 1
FlexCAN_T4<CAN2, RX_SIZE_256, TX_SIZE_16>     canBus;  // can1 port

int local_name = 0;
int msg_array[8] = {1, 2, 3, 4, 32, 6, 7, 8};
int state;
uint32_t timer;

//Key pins
const int KEY_PIN_01 = 6;
const int KEY_PIN_02 = 7;
const int KEY_PIN_03 = 8;
const int KEY_PIN_04 = 9;

const int LED_FD = 22; //22
const int LED_16 = 23; //23

const int MOTOR_ID = 0;

//----------------------------------------------------------------
void setup(void) {
  Serial.begin(115200);
  delay(500);
  Serial.println("Client CAN Bus FD and CAN BUS 1");

  //---------------------------------------
  int muxCounter = 0;
  while (muxCounter != 3) {
    if (!sx03.begin(SX1509_ADDRESS_11) ) {
      Serial.print("Failed 03");
      Serial.print(" " + SX1509_ADDRESS_11);
      Serial.print(" ");
      Serial.println(muxCounter);
      delay(100);
      muxCounter++;
    } else {
      Serial.println("Connected 03");
      Serial.print("" + SX1509_ADDRESS_11);
      Serial.print(" ");
      Serial.println(muxCounter);
      break;
    }
  }
  muxCounter = 0;
  delay(200);

  sx03.pinMode(STATUS_PIN_SX03, OUTPUT);
  sx03.digitalWrite(STATUS_PIN_SX03, HIGH);
  delay(500);
  sx03.digitalWrite(STATUS_PIN_SX03, LOW);


  //setup CAN 0 BUS
  canBus.begin();
  canBus.setBaudRate(500000);     // 500kbps data rate
  canBus.enableFIFO();
  canBus.enableFIFOInterrupt();
  canBus.onReceive(FIFO, canBusSniff);
  canBus.mailboxStatus();

  //setup CAN FD bus
  FD.begin();
  CANFD_timings_t config;
  config.clock = CLK_40MHz; //40. CLK_80MHz
  config.baudrate = 1000000;
  config.baudrateFD = 8000000;
  config.propdelay = 190;
  config.bus_length = 1;
  config.sample = 87.5;
  FD.setRegions(64);
  FD.setBaudRate(config);
  FD.mailboxStatus();

  //Key values
  pinMode(KEY_PIN_01, INPUT);
  pinMode(KEY_PIN_02, INPUT);
  pinMode(KEY_PIN_03, INPUT);
  pinMode(KEY_PIN_04, INPUT);

  //turn on LEDs
  pinMode(LED_FD, OUTPUT);
  pinMode(LED_16, OUTPUT);

  digitalWrite(LED_FD, HIGH); //CAN Bus FD
  digitalWrite(LED_16, HIGH); //CAN Bus 2.0
  delay(1000);

  digitalWrite(LED_FD, LOW);
  digitalWrite(LED_16, LOW);

  state = HIGH;
  timer = millis();

  Serial.println("Init client done");
}

//----------------------------------------------------------------
void loop() {
  CANFD_message_t msg;
  sx03.digitalWrite(STATUS_PIN_SX03, LOW);
  digitalWrite(LED_FD, LOW); 

  if (FD.read(msg)) {
    Serial.println(" ");
    reading(msg);
    sx03.digitalWrite(STATUS_PIN_SX03, HIGH);
    digitalWrite(LED_FD, HIGH); 
  }
  
}

//----------------------------------------------------------------
void canBusSniff(const CAN_message_t &msg) { // global callback
  digitalWrite(LED_FD, HIGH);

  Serial.print("T4: ");
  Serial.print("MB "); Serial.print(msg.mb);
  Serial.print(" OVERRUN: "); Serial.print(msg.flags.overrun);
  Serial.print(" BUS "); Serial.print(msg.bus);
  Serial.print(" LEN: "); Serial.print(msg.len);
  Serial.print(" EXT: "); Serial.print(msg.flags.extended);
  Serial.print(" REMOTE: "); Serial.print(msg.flags.remote);
  Serial.print(" TS: "); Serial.print(msg.timestamp);
  Serial.print(" ID: "); Serial.print(msg.id, HEX);
  Serial.print(" IDHIT: "); Serial.print(msg.idhit);

  Serial.print(" Buffer: ");
  for ( uint8_t i = 0; i < msg.len; i++ ) {
    Serial.print(msg.buf[i], HEX); Serial.print(" ");
  } Serial.println();

  digitalWrite(LED_FD, LOW); //CAN Bus FD

}

//----------------------------------------------------------------
void reading(CANFD_message_t msg) {
  //turn on LED
  digitalWrite(LED_FD, HIGH);
  int node = msg.id & 0xF;
  int local = (msg.id >> 4) & 0xF;
  //print CAN BUS data
  Serial.print("  ID: ");
  Serial.print("  Node: ");
  Serial.print(node);
  Serial.print("  Local: ");
  Serial.print(local);
  Serial.print("  LEN: ");
  Serial.print(msg.len);
  Serial.print(" DATA: ");

  for ( uint8_t i = 0; i < msg.len; i++ ) {
    Serial.print(msg.buf[i]);
    Serial.print(" ");
  }

  //turn off LED
  digitalWrite(LED_FD, LOW);
}

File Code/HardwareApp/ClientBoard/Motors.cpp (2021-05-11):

#include "Motors.h"



Motors::Motors() {

}


void Motors::init() {


  upperStepLimit = 100;

  SERIAL_PORT.begin(250000);

  delay(1000);
  initializeMotorSX();


  driver.begin();

  Serial.println("Initializing Motors...");
  for (int i = 0; i < MOTORS_PER_PANEL; i++) {
    currentStep[i] = 0;
    shaftDir[i] = true;

    enableMotor(i);
    setUpMotor(i);

    activeMotors[i] = true;
    stepTarget[i] = 0;
  }
}


void Motors::initializeMotorSX() {
  int muxCounter = 1;

  Serial.println("starting motors");
  while (muxCounter != 3) {
    if (!sx.begin(SX1509_ADDRESS_00) ) {
      Serial.print("Failed 00 ");
      Serial.print(SX1509_ADDRESS_00);
      Serial.print(" ");
      Serial.println(muxCounter);
      delay(100);
      muxCounter++;
    } else {
      Serial.println("Connected 00");
      Serial.print(SX1509_ADDRESS_00);
      Serial.print(" ");
      Serial.println(muxCounter);
      break;
    }
  }


  setupSXPins();
}


// The function that runs in the main loop of the program. This function manually steps through each motor based on the current instruction given via CANBUS.
void Motors::motorInstructionLoop() {

  if (activeMotors[0]) digitalWrite(STEP_PIN_01, HIGH);
  if (activeMotors[1]) digitalWrite(STEP_PIN_02, HIGH);
  if (activeMotors[2]) digitalWrite(STEP_PIN_03, HIGH);
  if (activeMotors[3]) digitalWrite(STEP_PIN_04, HIGH);
  if (activeMotors[4]) digitalWrite(STEP_PIN_05, HIGH);
  if (activeMotors[5]) digitalWrite(STEP_PIN_06, HIGH);
  if (activeMotors[6]) digitalWrite(STEP_PIN_07, HIGH);
  if (activeMotors[7]) digitalWrite(STEP_PIN_08, HIGH);
  delayMicroseconds(64);

  if (activeMotors[0]) digitalWrite(STEP_PIN_01, LOW);
  if (activeMotors[1]) digitalWrite(STEP_PIN_02, LOW);
  if (activeMotors[2]) digitalWrite(STEP_PIN_03, LOW);
  if (activeMotors[3]) digitalWrite(STEP_PIN_04, LOW);
  if (activeMotors[4]) digitalWrite(STEP_PIN_05, LOW);
  if (activeMotors[5]) digitalWrite(STEP_PIN_06, LOW);
  if (activeMotors[6]) digitalWrite(STEP_PIN_07, LOW);
  if (activeMotors[7]) digitalWrite(STEP_PIN_08, LOW);
  delayMicroseconds(64);

  // Update the step counters for all motors;
  for (int i = 0; i < MOTORS_PER_PANEL; i++) {
    if (activeMotors[i]) {
      int change = (shaftDir[i]) ? 1:-1;
      currentStep[i] += change;

      // Check upper bound of pixel
      if (upperStepLimit - currentStep[i] < MOTOR_STEP_TOLERANCE) {
        currentStep[i] = upperStepLimit;
        stopMotor(i);
      }

      // Check lower bound of pixel
      if (currentStep[i] < MOTOR_STEP_TOLERANCE){
        stopMotor(i);
        currentStep[i] = 0;
      }


      // Check target Position against target to know when to stop
      if (abs(currentStep[i] - stepTarget[i]) < MOTOR_STEP_TOLERANCE) {
        currentStep[i] = stepTarget;
        stopMotor(i);
      }

    }
  }
}

int Motors::getMotorTargetPos(int id) {
  return stepTarget[id];
}

void Motors::setMotorTarget(int id, int targetPos, int tolerance = MOTOR_STEP_TOLERANCE) {
  int dist = targetPos - currentStep[id];

  if (abs(dist) < tolerance) {
    stopMotor(id);
    return;
  }

  stepTarget[id] = targetPos;

  activeMotors[id] = true; // Lets the motor move;

  if (dist < 0) {
    shaftDir[id] = false; // Going Down
  } else {
    shaftDir[id] = true; // Going Up
  }

  enableMotor(id);
  driver.shaft(shaftDir[id]);
  testConnection(0);
}

void Motors::testConnection(int id) {
  int result = driver.test_connection();
  Serial.print(F("Conn: "));
  Serial.print(id);
  Serial.print(F(" "));
  Serial.println(result);
}


void Motors::stopMotor(int id) {
  // TODO: DISABLE MOTORS POWER

  // sx.digitalWrite(smthg, HIGH);

  activeMotors[id] = false;
}

int Motors::getMotorCurrentStep(int id) {
  return currentStep[id];
}

bool Motors::getMotorDir(int id) {
  return shaftDir[id]; // false is down, true is up
}

// Returns whether or not the current motor is moving.
bool Motors::isActive(int id) {
  return activeMotors[id];
}

int Motors::getUpperStepLimit() {
  return upperStepLimit;
}

void Motors::setUpperStepLimit(int stepLimit) {
  upperStepLimit = stepLimit;
}

void Motors::enableMotor(int id) {
  switch(id) {
    case 0:
      sx.digitalWrite(selectMotor[0], LOW);
      sx.digitalWrite(selectMotor[1], LOW);
      sx.digitalWrite(selectMotor[2], LOW);
      break;
    case 1:
      sx.digitalWrite(selectMotor[0], HIGH);
      sx.digitalWrite(selectMotor[1], LOW);
      sx.digitalWrite(selectMotor[2], LOW);
      break;
    case 2:
      sx.digitalWrite(selectMotor[0], LOW);
      sx.digitalWrite(selectMotor[1], HIGH);
      sx.digitalWrite(selectMotor[2], LOW);
      break;
    case 3:
      sx.digitalWrite(selectMotor[0], HIGH);
      sx.digitalWrite(selectMotor[1], HIGH);
      sx.digitalWrite(selectMotor[2], LOW);
      break;
    case 4:
      sx.digitalWrite(selectMotor[0], LOW);
      sx.digitalWrite(selectMotor[1], LOW);
      sx.digitalWrite(selectMotor[2], HIGH);
      break;
    case 5:
      sx.digitalWrite(selectMotor[0], HIGH);
      sx.digitalWrite(selectMotor[1], LOW);
      sx.digitalWrite(selectMotor[2], HIGH);
      break;
    case 6:
      sx.digitalWrite(selectMotor[0], LOW);
      sx.digitalWrite(selectMotor[1], HIGH);
      sx.digitalWrite(selectMotor[2], HIGH);
      break;
    case 7:
      sx.digitalWrite(selectMotor[0], HIGH);
      sx.digitalWrite(selectMotor[1], HIGH);
      sx.digitalWrite(selectMotor[2], HIGH);
      break;
  }
}

void Motors::setUpMotor(int id) {
  driver.toff(5);                 // Enables driver in software
  driver.rms_current(500);        // Set motor RMS current
  driver.microsteps(32);          // Set microsteps to 1/16th

  //driver.en_pwm_mode(true);       // Toggle stealthChop on TMC2130/2160/5130/5160
  driver.en_spreadCycle(false);   // Toggle spreadCycle on TMC2208/2209/2224
  driver.pwm_autoscale(true);     // Needed for stealthChop

  Serial.print(F("\nTesting connection... "));
  Serial.println(id);
  uint8_t result = driver.test_connection();
  delay(200);
  if (result) {
    Serial.println(F("failed!"));
    Serial.print(F("Likely cause: "));
    switch (result) {
      case 1: Serial.println(F("loose connection")); break;
      case 2: Serial.println(F("Likely cause: no power")); break;
    }
    Serial.println(F("Fix the problem and reset board."));
    // abort();
  }
  Serial.println(F("OK"));

}
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

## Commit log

2020-07-08 transfer repo
    [2020-01-03T130948_newBoard.csv, 2020-02-20T134944.csv, 32-pin QFN+TQFP.brd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]
2020-07-13 clean up interactive board and motor controller
    [2020-01-03T130948_newBoard.csv, MotorControl.brd, MotorControl.sch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]
2020-07-13 updated circuit box
2020-07-13 readme circuit
2020-07-13 git ignore
    [2020-01-03T130948_newBoard.csv, 2020-02-20T134944.csv, 32-pin QFN+TQFP.brd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]
2020-07-13 CAN Bus
2020-07-13 can bus clean test codes
2020-07-14 A document on motor to motor controller board hookup
2020-07-14 updated submodule to track roboscope_websocket branch
2020-07-15 documentation for CAN BUS FD 2.0
2020-08-06 Applied motor interrupts to the client board script
2020-08-06 Reverted to older interface code due to a bug
    [InterfacePanel.cpp]
2020-08-09 made ID_to_table work for more general case and added table settings
2020-08-13 CAN bus FD interrupts and receiving entire table information working
2020-08-20 updated location dwg
    [Interactive Table (Rev 5 200114).dwg]
2020-09-27 update scaling alg, add height, matched seriallib to teensy code
2020-11-03 Updated the client board to include neopixels
2020-11-05 CanBus_LEDs test
2020-11-05 enable Motor
    [DRILEGEND.CFG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]
2020-11-17 include motor pins
2020-11-17 clean circuit
    [DRILEGEND.CFG, InteractionBoard.brd, InteractionBoard.sch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]
2020-11-19 canbus_leds test update
2020-11-19 update CanBus readme and instructions
2020-11-30 Updated ClientBoard to disable motors (Haven't been unit tested)
2021-01-07 Added check for node id and bug fix
    [ClientBoard.ino]
2021-01-18 update circuits
    [2020-01-03T130948_newBoard.csv, InteractionBoard.brd, InteractionBoard.dwg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]
2021-01-18 clean hardware file
    [2x2 Base Supports 200921.dwg, 2x2 Base Supports 200921.dxf, 4X4TOP.dwg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]
2021-01-24 motor board update
2021-01-25 clean traces and silscreen
    [MotorControl_M.brd, MotorControl_M.sch]
2021-03-15 updated CanBusLEDs
2021-04-02 Added TMC Stepper library to repo
    [Register_summary.xlsx, TMC5130_TMC2130_TMC2100_Calculations.xlsx]
2021-04-02 Added AccelStepper library to repo
    [project.cfg]
2021-04-02 Removed incorrect AccelStepper library
    [project.cfg]
2021-04-09 update motors
    [InteractionBoard.brd, LEDBox.brd, LEDBox.sch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]
2021-04-09 Fixed bug in nonblocking test code for motor
2021-04-16 Updated clientboard to use TMC Drivers.
2021-04-16 Added motor util functions
2021-04-30 A real quick calibration board test (Wrong pins)
2021-04-30 calibration board test should use correct pins
2021-04-30 More updates to client board motor controls
2021-04-30 Added limits to motor movement
2021-04-30 More client board updates with stronger limits
2021-04-30 calibration board test
2021-05-11 Fixed bug in getting target position of motors
    [Motors.cpp, Motors.h]
2021-05-11 Fixed misc bugs in client board
    [BoardPins.h, ClientBoard.ino, InterfacePanel.cpp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]
2021-05-11 updated motor library
2021-07-14 update sockets
2021-07-21 motor controll
2023-05-10 members w update
    [A1.obj, A10.obj, A11.obj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]
2023-06-26 message+motor
    CAN bus message structure changed, initialize motor position
2023-07-28 using teensy 4.1
    [CANBUS_USB_Updated v3.brd, CANBUS_USB_Updated_v6.sch]
2023-07-31 server board w/ teensy 4.1
    [CANBUS_USB_TEENSY_41.brd, CANBUS_USB_TEENSY_41.sch]
2023-08-02 added hall effect in place of button
    [InteractionBoard_HallEffect.brd, InteractionBoard_HallEffect.sch]
2023-08-03 added sparkfun.dru rule
    [CANBUS_USB_TEENSY_41.brd]
2023-08-08 manually routed
    [InteractionBoard_HallEffect.brd]
2023-08-09 less unused space
    [InteractionBoard_HallEffect.brd]
2023-08-09 fixed board usb
    [2023-04-13T105801.csv]
2023-08-09 connected ground
    [InteractionBoard_HallEffect.brd]
2023-08-09 Serial Update, Pin Change

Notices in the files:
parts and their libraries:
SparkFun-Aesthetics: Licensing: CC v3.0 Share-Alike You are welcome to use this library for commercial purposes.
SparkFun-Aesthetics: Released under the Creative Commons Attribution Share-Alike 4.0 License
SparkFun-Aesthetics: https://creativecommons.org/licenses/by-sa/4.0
